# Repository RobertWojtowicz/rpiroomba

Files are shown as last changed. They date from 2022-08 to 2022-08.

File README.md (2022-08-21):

# RPiRoomba

## 1. Introduction
This project is based on the following projects:
- https://github.com/pomeroyb/Create2Control
- https://github.com/silvanmelchior/RPi_Cam_Web_Interface

## 2. How does this work?
- the project applies only to Roomba models that have 7-pin Mini-DIN serial port (iRobot Create Intereface);
- please note that different Roomba models have in different places this port, the PCB was designed for the Roomba 620;
- in case of Roomba 620 you have to cut a hole in the bezel to get to Mini-DIN serial port (the bezel is replaceable, in different colors ;-) to remove the bezel follow the instructions in this project: https://github.com/joric/joirc;
- the port was connected through a logical level converter together with Raspberry Pi Zero W;
- Raspberry Pi Zero W was connected to the camera, LED driver and micro servo, as in the images below:
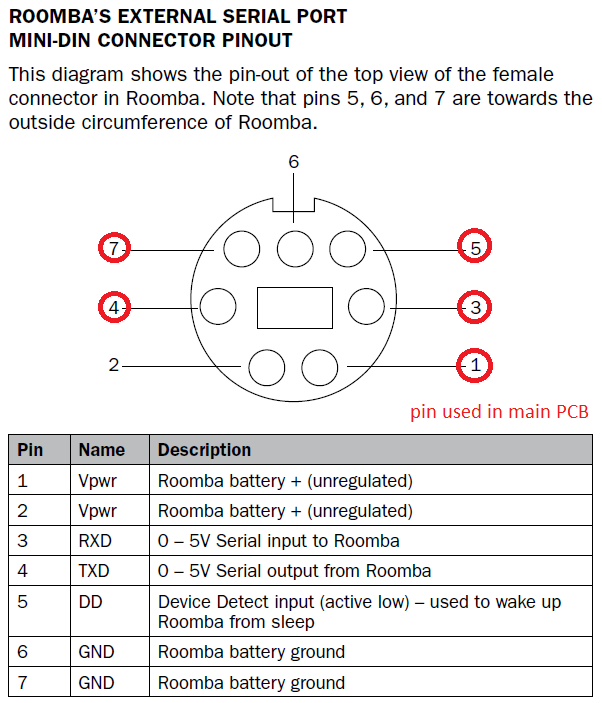
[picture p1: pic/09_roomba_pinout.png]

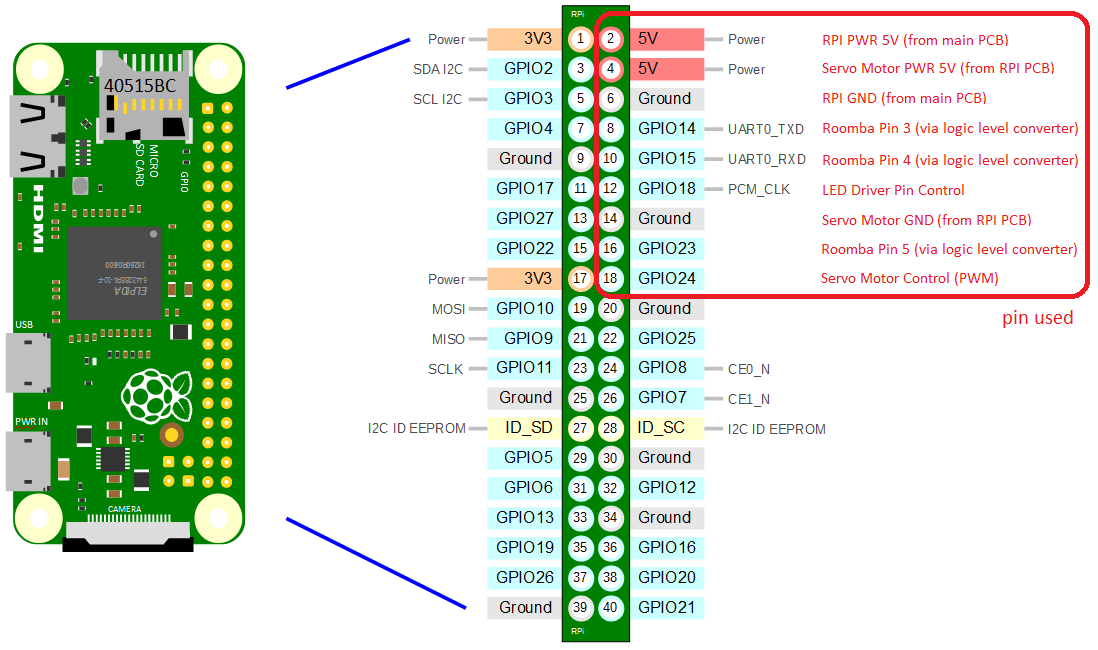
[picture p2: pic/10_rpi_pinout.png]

- the project allows you to remotely control Roomba (via WiFi), watch live video and record, take pictures;
- it is possible to run a cleaning schedule, which Roomba 620 does not have;
- infrared high power LED chip allows visibility of the camera at night;
- it is possible to adjust the camera position angle (0°, 30°, 60°, 90°).

## 3. Build hardware
- create your own PCB v1.1 according to the project files: roomba_led_pcb_v1.sch, roomba_led_pcb_v1.brd, roomba_main_pcb_v1.sh, roomba_main_pcb_v1.brd from this repository (files location: rpiroomba/pcb/), example of finished PCBs v1.0 below:
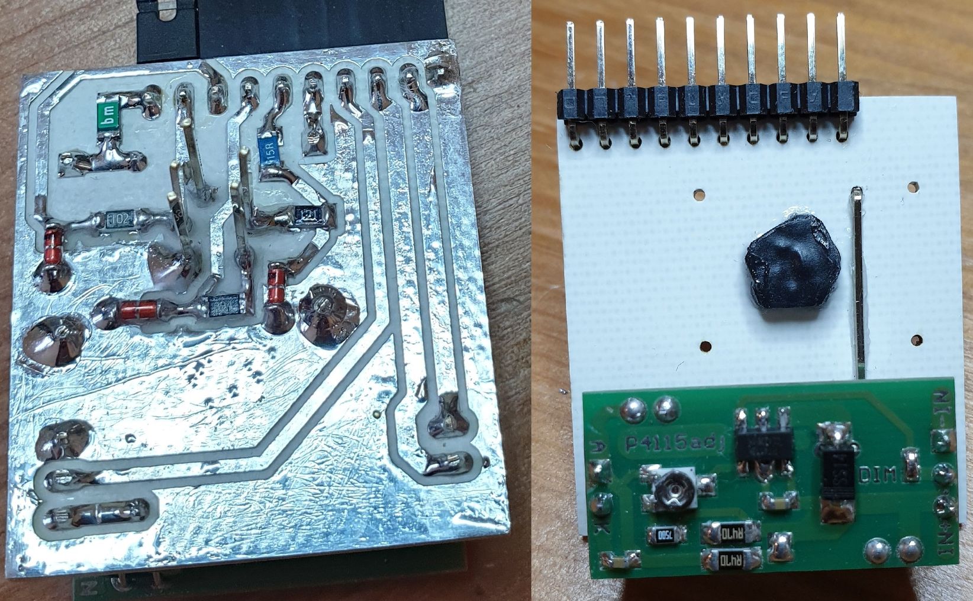
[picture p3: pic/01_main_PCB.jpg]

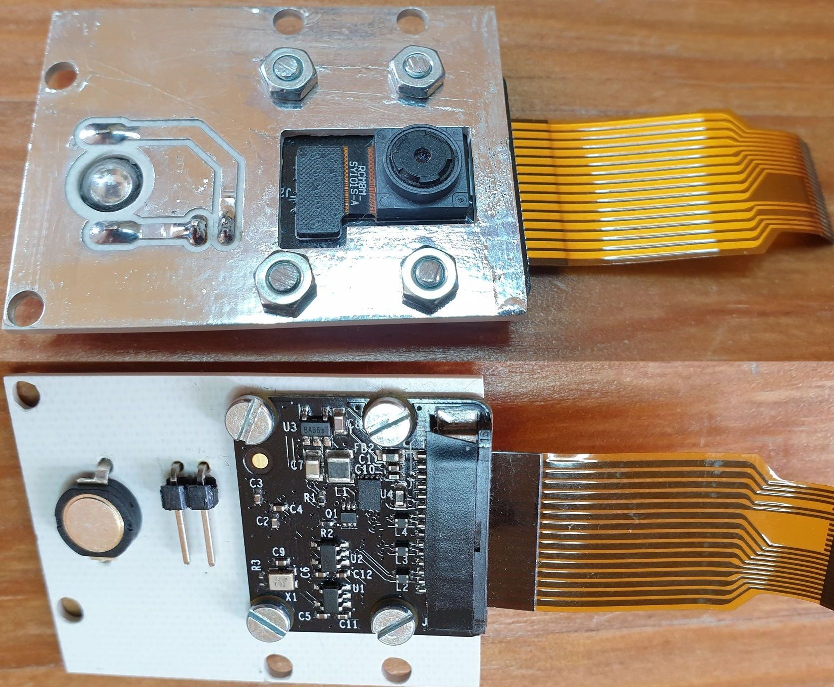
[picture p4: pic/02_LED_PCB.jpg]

- prepare the aluminium housing - heat sink for CPU Raspberry Pi Zero W and high power LED chip, similar to the picture (dimensions approx: 36 mm x 65 mm):
- add a thermal pad under the high power LED chip and the CPU Raspberry Pi Zero W to dissipate the heat to the aluminium case;
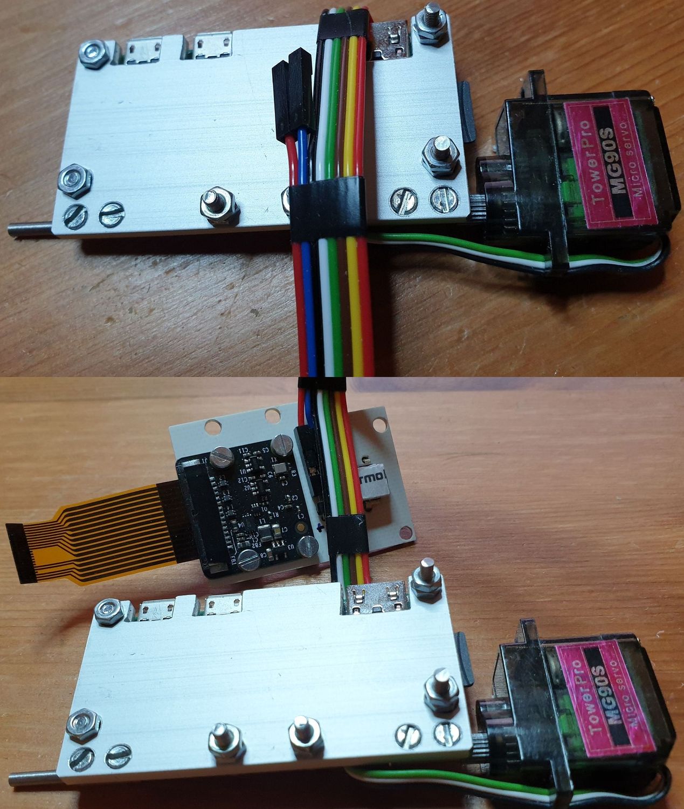
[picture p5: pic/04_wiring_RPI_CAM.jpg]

- the hinges come from the elements of the electric cube;
- metric screws with a diameter of 2 mm were used to connect the parts;
- reduce the current on the LED driver from 700 mA to 230 mA (too high power causes unreadable view);
- set a voltage of 5V on the step-down DC/DC module;
- isolate the Raspberry Pi and camera pins from accidental short circuits, as shown in the following picture:
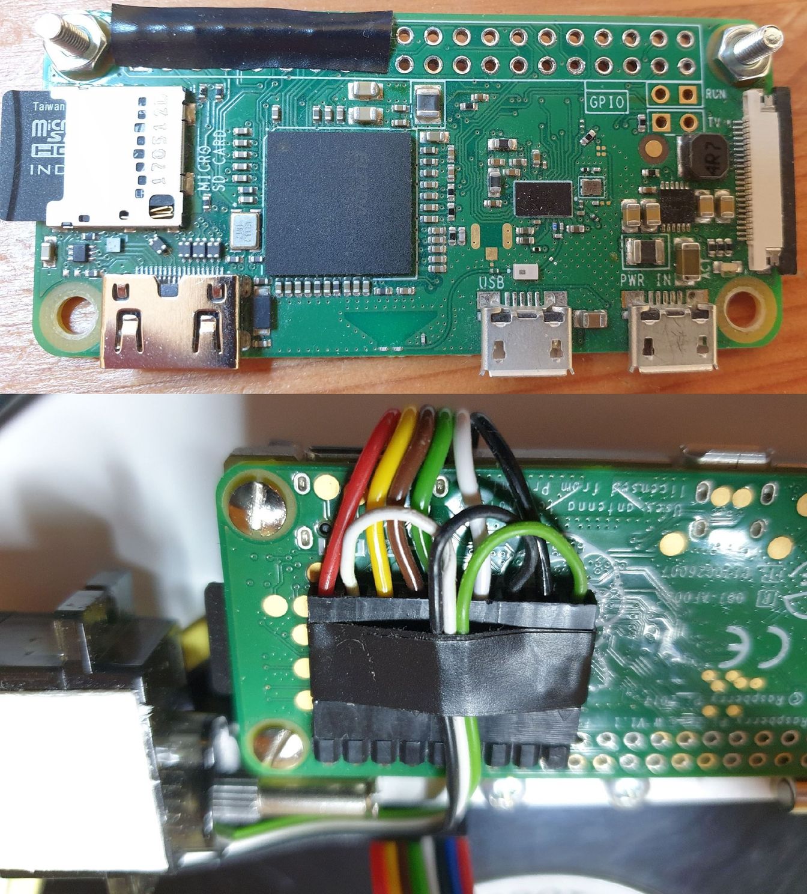
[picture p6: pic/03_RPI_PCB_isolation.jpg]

- isolate the IR sensor on the Roomba in half with tape, as shown in the following picture (otherwise the docking station search algorithm will fail when the Raspberry Pi Zero W module is installed):
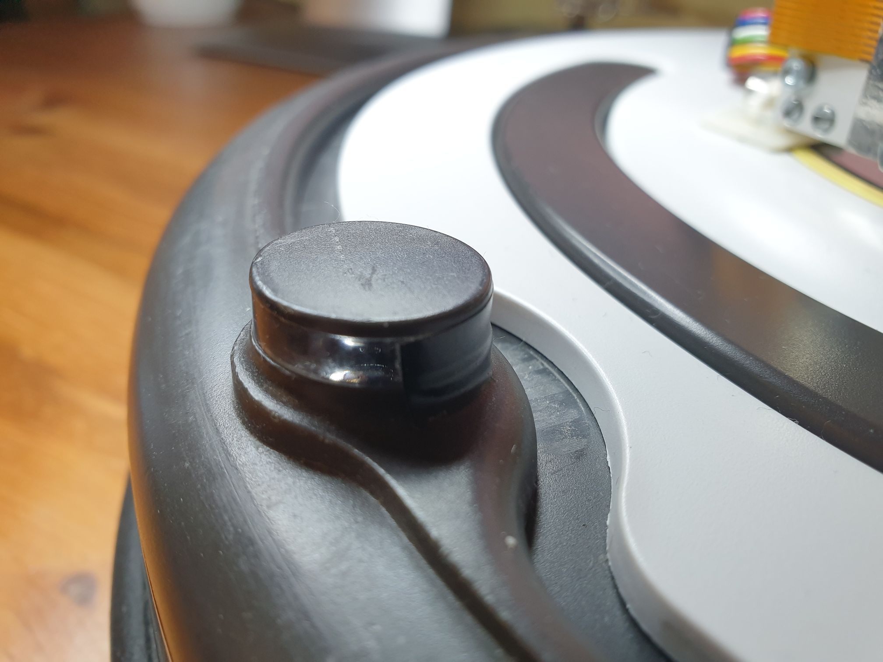
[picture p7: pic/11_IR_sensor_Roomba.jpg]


The following parts are required:
- Modules: 1x DC/DC step-down MP1584EN, 1x Raspberry Pi Zero W V1.1, 1x Raspberry Pi NoIR Camera V2, 1x LED driver PT4115:<br>

- 1x Camera adaptor (cable) from official case Raspberry Pi Zero;
- 1x Micro servo TowerPro MG90S;
- 1x SMD 1206 high power LED chip, 3W IR 850 Nm;
- 1x SMD 1206 resettable polymeric fuse 500 mA;
- 1x SMD 1206 resistors: 15 Ohm, 120 Ohm, 390 Ohm, 1 kOhm;
- 3x SMD 1206 zener diode 3.3 V;
- 1x 40 pin, 2.54 mm, single in line, 20 mm long, header male;
- 1x 40 pin, 2.54 mm, single in line, right angle, header male.

## 4. Preparing Linux system (tested on current kernel 5.15.56+)
- download Raspberry Pi OS (32-bit) Lite system image: https://downloads.raspberrypi.org/raspios_lite_armhf_latest;
- upload system to the microSD card, using Raspberry PI Imager, all you need is a 4 GB microSD card with UHS-1 speed class;
- in Raspberry PI Imager advanced options, set: Enable SSH, Set username and password, Configure wireless LAN;
- on the boot partition replace or edit "config.txt" file based on an example from this repository (file location: /rpi/boot/);
- to disable HDMI (to reduce the power consumption) you must replace or edit "rc.local" file based on an example from this repository (file location: rpiroomba/rpi/etc/);
- install modules: sudo apt-get install python3-pip, sudo pip install pyserial.

## 5. Installing RPi-CAM-Web-Interface (tested on current version 6.6.26)
To install RPi-CAM-Web-Interface, run the following commands:
- sudo apt-get install git;
- git clone https://github.com/silvanmelchior/RPi_Cam_Web_Interface.git;
- cd RPi_Cam_Web_Interface;
- ./install.sh;
- in the configuration menu, clear the "xCam subfolder" option, add the user in "xUser:" admin and the password "xPassword:" and select OK;
- when the installation is complete you can delete folder, rm -rf RPi_Cam_Web_Interface;
- change the autostart parameter to idle in /etc/raspimjpeg (to disable the automatic start of the camera when starting Raspberry Pi);
- change the parameters in the browser under Camera Settings to: Load Preset: HD-ready 720p, Rotation: Rotate_270, Preview quality: Quality: 10, Width 1280, Divider: 1, for example picture of RPI Cam interface:
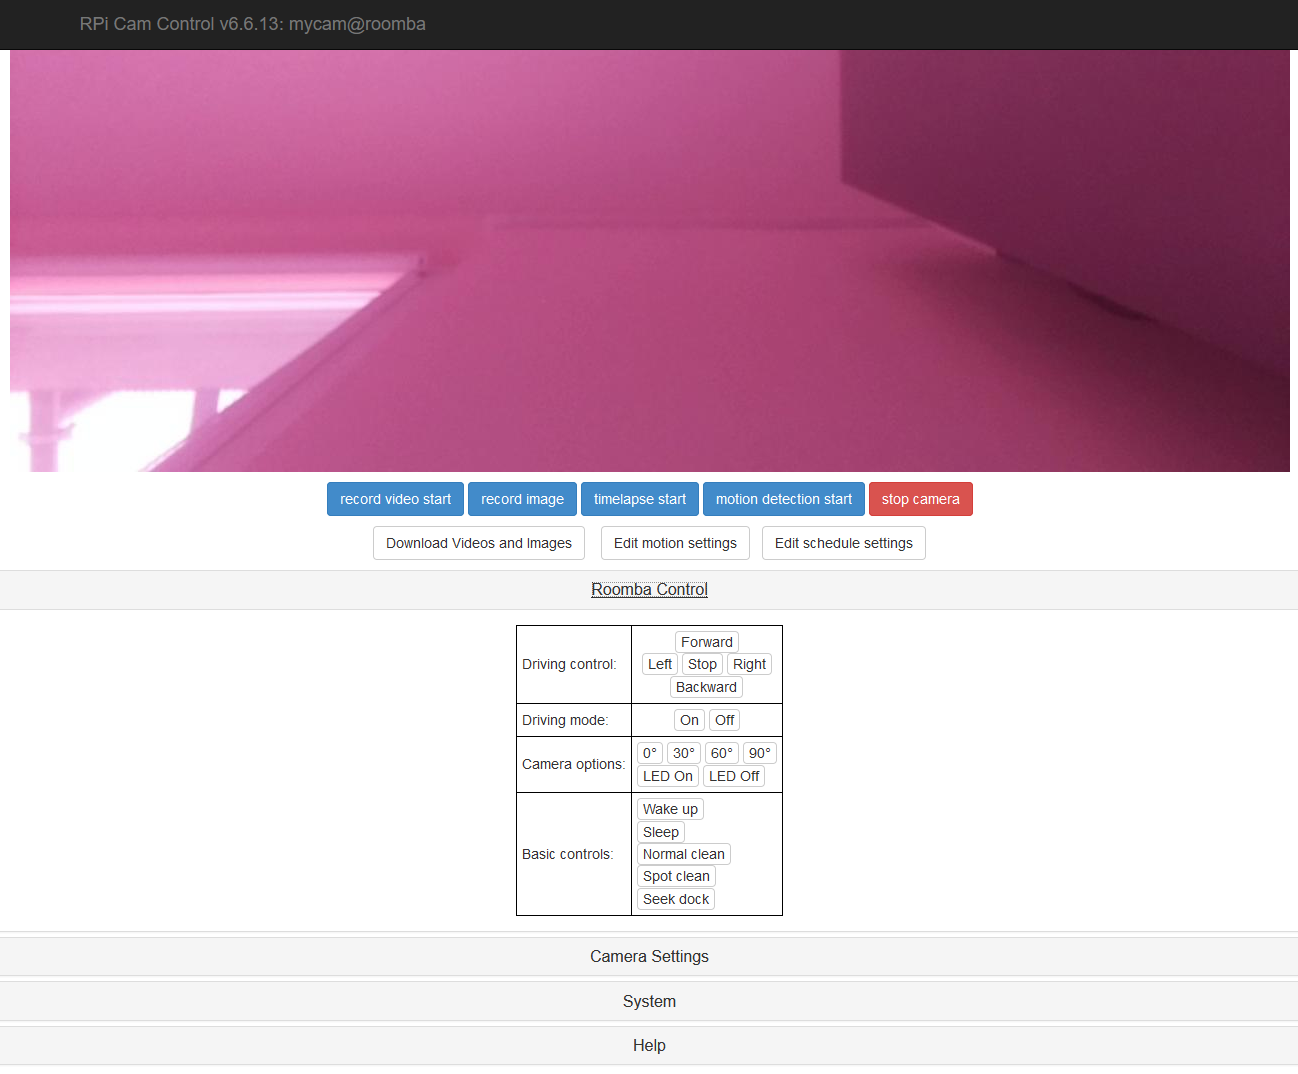
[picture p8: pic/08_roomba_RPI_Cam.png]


## 6. Configuring scripts
- create a roomba folder in /var/www/ directory and then copy the files, e.g. using WinSCP from this repository (file location: /rpi/www/roomba/): command.php, config.json, create2api.py, jquery-3.6.0.min.js, roomba.py, submit.js;
- in /var/www/ directory, you should replace index.html from this repository (file location: /rpi/www/);
- grant permissions for user-data: sudo usermod -a -G gpio www-data, sudo usermod -a -G gpio $USER, sudo usermod -a -G dialout www-data;
- grant permissions to execute files, chmod +x /var/www/roomba/*

## 7. Creating a cleaning schedule
- Roomba 620 does not have its own cleaning schedule, but you can add in cron;
- for example, Monday, Wednesday, Friday at 12:00 you should edit the file using the command crontab -e:<br/> 
00 12 * * 1 python3 /var/www/roomba/roomba.py clean<br/>
00 12 * * 3 python3 /var/www/roomba/roomba.py clean<br/>
00 12 * * 5 python3 /var/www/roomba/roomba.py clean

## 8. Some final project photos
- Camera down (position angle 0°):
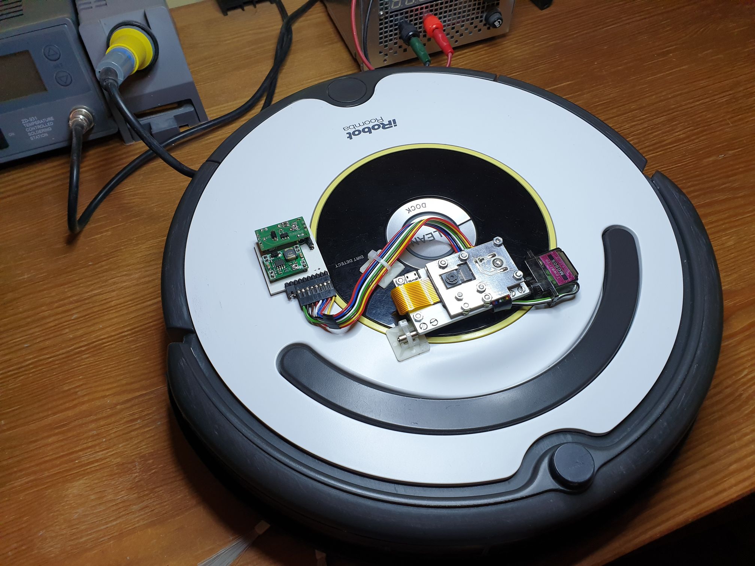
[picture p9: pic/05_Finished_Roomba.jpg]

- Current limit adjustment on LED driver:
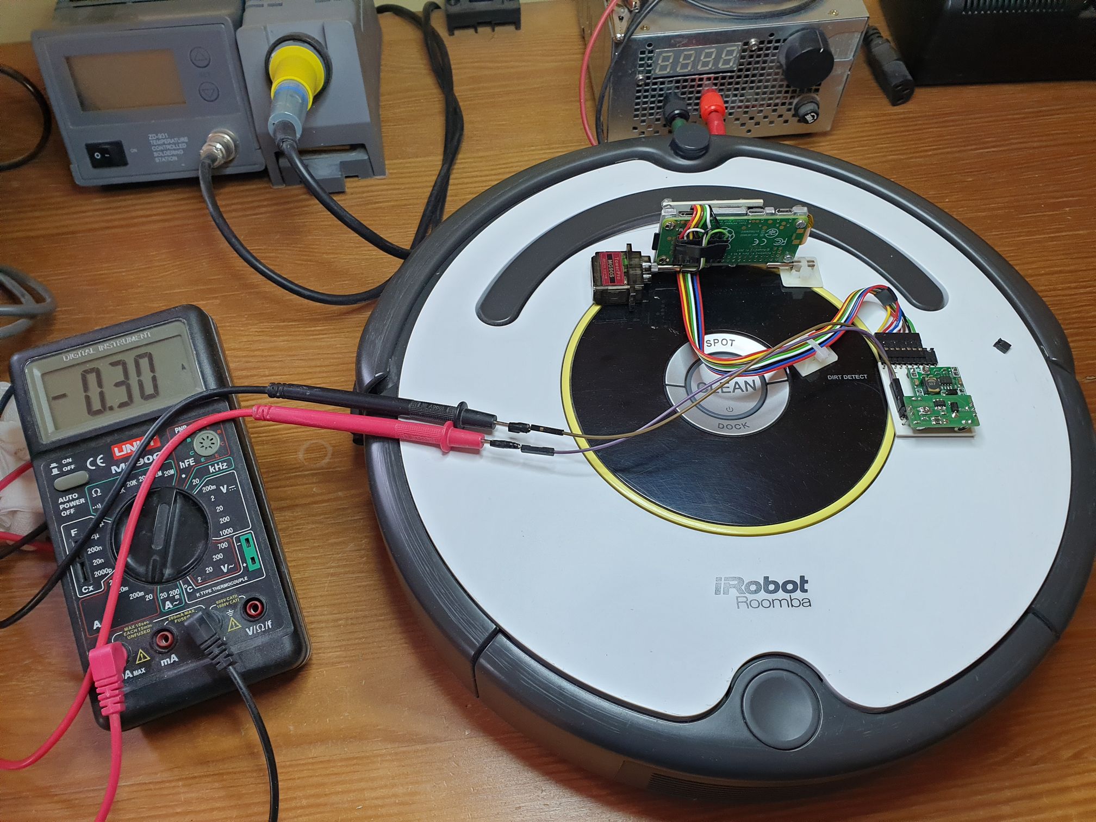
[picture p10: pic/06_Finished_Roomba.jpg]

- Camera up (position angle 90°):
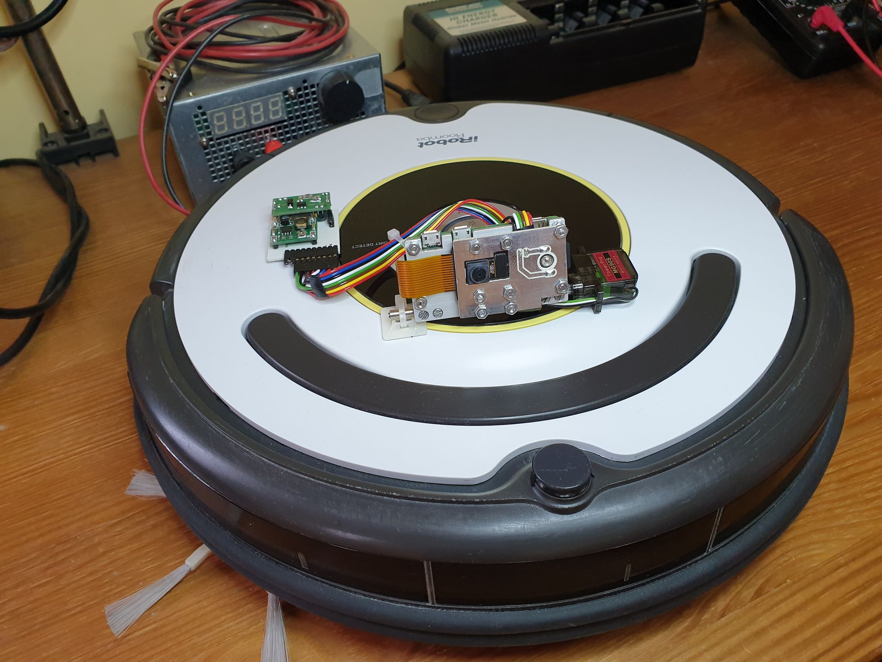
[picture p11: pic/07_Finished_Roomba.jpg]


<a href="https://www.buymeacoffee.com/RobertWojtowicz" target="_blank">Buy Me A Coffee</a>

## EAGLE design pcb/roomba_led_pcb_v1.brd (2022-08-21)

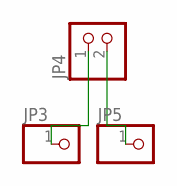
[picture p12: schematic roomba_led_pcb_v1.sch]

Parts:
JP3, JP5: PINHD-1X1; 1X01
JP4: PINHD-1X2/90; 1X02/90

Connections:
unnamed: JP3.1, JP4.1
unnamed: JP4.2, JP5.1

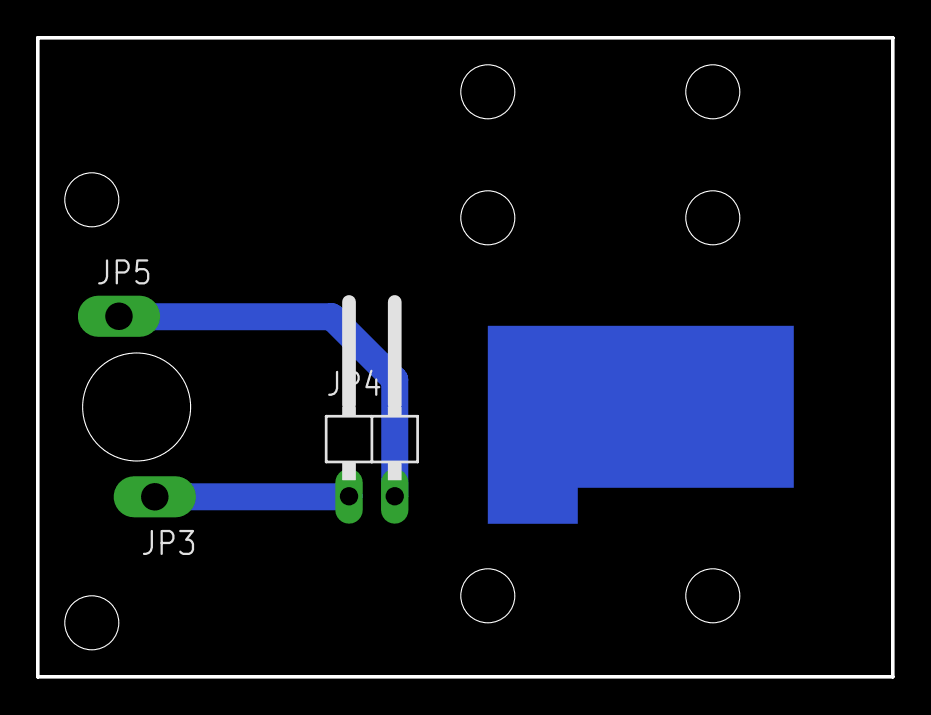
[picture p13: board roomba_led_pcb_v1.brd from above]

Board: 2 copper layers, 47.5 x 35.5 mm, 3 parts (0 on the bottom side), 2 nets.

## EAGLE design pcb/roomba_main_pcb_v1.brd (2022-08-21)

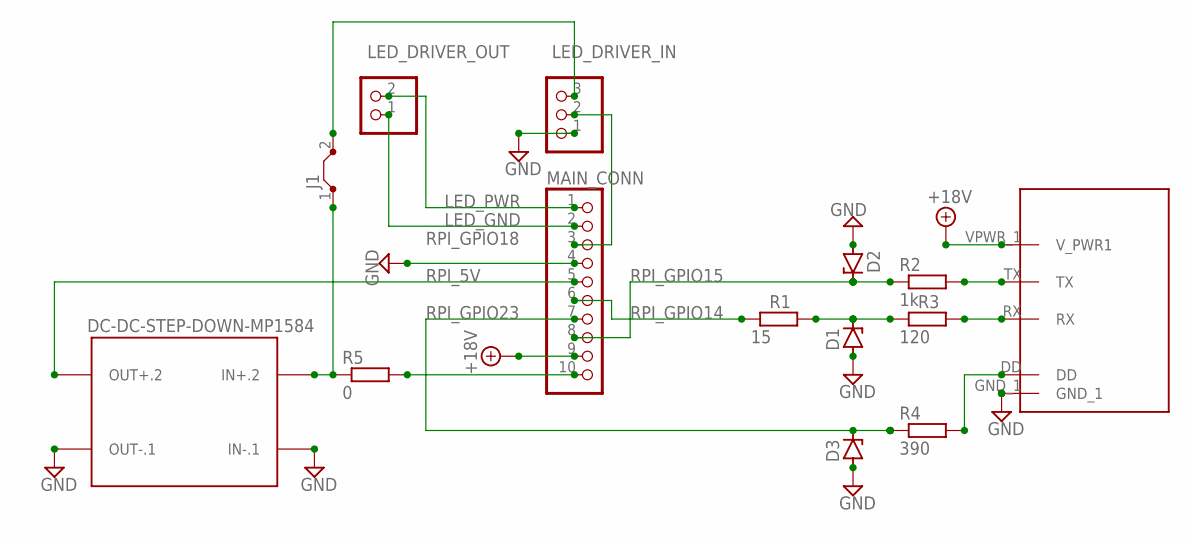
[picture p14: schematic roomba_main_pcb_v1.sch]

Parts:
D1, D2, D3: ZENER-DIODESOD80C; SOD80C
J1: J25MM; 25
LED_DRIVER_IN: PINHD-1X3; 1X03
LED_DRIVER_OUT: PINHD-1X2; 1X02
MAIN_CONN: PINHD-1X10/90; 1X10/90
R1: 15; M1206
R2: 1k; M1206
R3: 120; M1206
R4: 390; M1206
R5: 0; M1206
ROOMBA_PORT: 7_PIN; PIN-7
U$1: DC-DC-STEP-DOWN-MP1584

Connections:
+18V: MAIN_CONN.9, ROOMBA_PORT.VPWR_1 (V_PWR1)
GND: D1.A, D2.A, D3.A, LED_DRIVER_IN.1, MAIN_CONN.4, ROOMBA_PORT.GND_1, U$1.IN-.1, U$1.OUT-.1
LED_GND: LED_DRIVER_OUT.1, MAIN_CONN.2
LED_PWR: LED_DRIVER_OUT.2, MAIN_CONN.1
unnamed: J1.1, R5.1, U$1.IN+.2
unnamed: R4.2, ROOMBA_PORT.DD
unnamed: J1.2, LED_DRIVER_IN.3
unnamed: R3.2, ROOMBA_PORT.RX
unnamed: D1.C, R1.2, R3.1
unnamed: R2.2, ROOMBA_PORT.TX
unnamed: MAIN_CONN.10, R5.2
RPI_5V: MAIN_CONN.5, U$1.OUT+.2
RPI_GPIO14: MAIN_CONN.6, R1.1
RPI_GPIO15: D2.C, MAIN_CONN.8, R2.1
RPI_GPIO18: LED_DRIVER_IN.2, MAIN_CONN.3
RPI_GPIO23: D3.C, MAIN_CONN.7, R4.1

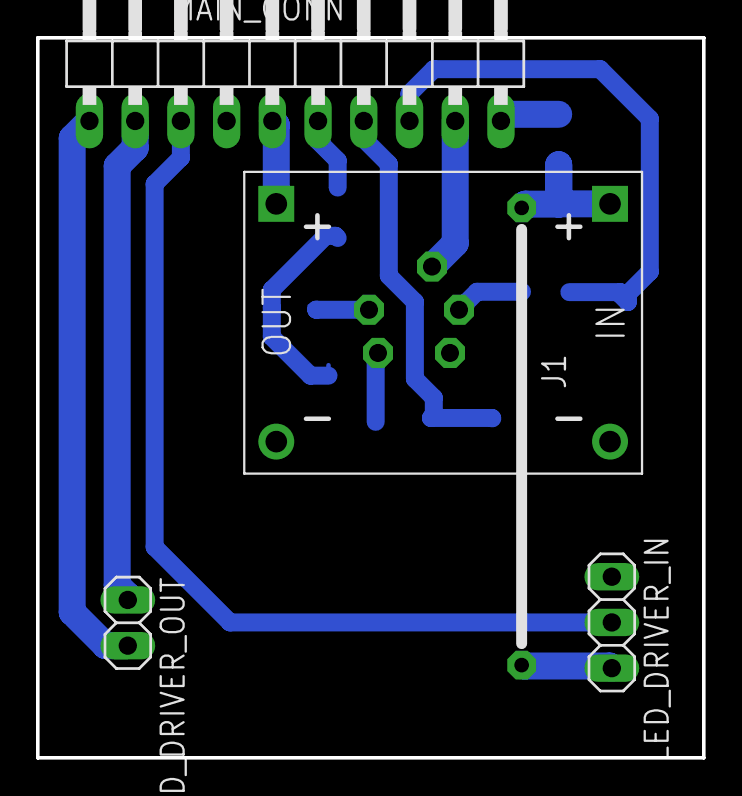
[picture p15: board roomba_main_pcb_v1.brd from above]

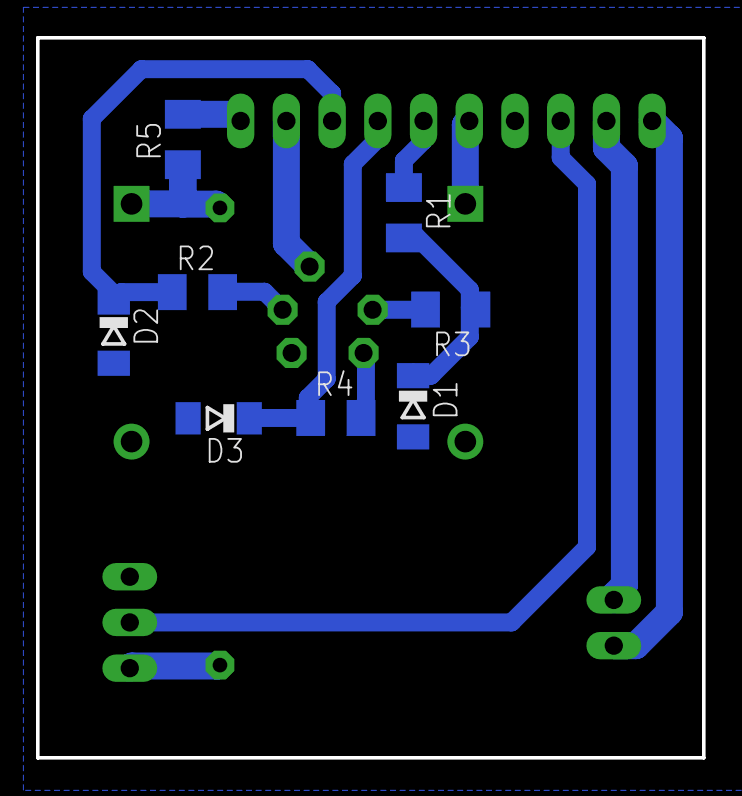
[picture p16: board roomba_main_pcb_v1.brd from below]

Board: 2 copper layers, 37.0 x 40.0 mm, 14 parts (8 on the bottom side), 16 nets.

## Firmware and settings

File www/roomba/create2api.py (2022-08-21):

#!/usr/bin/python

# Update to python3 for RPiRoomba v1.1

import json
import serial
import struct
import os
import warnings
import time

class Error(Exception):
    """Error"""
    pass

def custom_format_warning(message, category, filename, lineno, file=None, line=None):
    return 'Line ' + str(lineno) + ': ' + str(message) + '\n'
    #return ' %s:%s: %s:%s' % (filename, lineno, category.__name__, message)
    
class ROIDataByteError(Error):
    """Exception raised for errors in ROI data bytes.

        Attributes:
            msg -- explanation of the error
    """
    
    def __init__(self, msg):
        self.msg = msg

class ROIFailedToSendError(Error):
    """Exception raised when an error in data bytes prevented a packet to be sent

        Attributes:
            msg -- explanation of the error    
    """
    def __init__(self, msg):
        self.msg = msg

class ROIFailedToReceiveError(Error):
    """Exception raised when there is an error in the data received from the Create 2

        Attributes:
            msg -- explanation of the error
    """
    def __init__(self,msg):
        self.msg = msg


        
class Config(object):
    """This class handles loading and saving config files that store the
        Opcodes and other useful dicts
    
    """
    
    def __init__(self):
        self.fname = '/var/www/roomba/config.json'
        self.data = None
    
    def load(self):
        """ Loads a Create2 config file, that holds various dicts of opcodes.
        
        """
        if os.path.isfile(self.fname):
            #file exists, load it
            with open(self.fname) as fileData:
                try:
                    self.data = json.load(fileData)
                    print ('Loaded config and opcodes')
                except ValueError('e'):
                    print ('Could not load config')
        else:
            #couldn't find file
            print('No config file found')
            raise ValueError('Could not find config')

class SerialCommandInterface(object):
    """This class handles sending commands to the Create2.

    """

    def __init__(self):
        com = '/dev/ttyAMA0'  #This should not be hard coded...
        baud = 115200
        
        self.ser = serial.Serial()
        self.ser.port = com
        self.ser.baudrate = baud
        print(self.ser.name)
        if self.ser.isOpen(): 
            print('port was open')
            self.ser.close()
        self.ser.open()
        print('opened port')
    
    def send(self, opcode, data):
        #First thing to do is convert the opcode to a tuple.
        temp_opcode = (opcode,)
        bytes = None
        
        if data == None:
            #Sometimes opcodes don't need data. Since we can't add
            # a None type to a tuple, we have to make this check.
            bytes = temp_opcode
        else:
            #Add the opcodes and data together
            bytes = temp_opcode + data
        #print bytes
        self.ser.write(struct.pack('B' * len(bytes), *bytes))
    
    def Read(self, num_bytes):
        """Read a string of 'num_bytes' bytes from the robot.

            Arguments:
                num_bytes: The number of bytes we expect to read.
        """
        #logging.debug('Attempting to read %d bytes from SCI port.' % num_bytes)
        data = self.ser.read(num_bytes)
        #logging.debug('Read %d bytes from SCI port.' % len(data))
        if not data:
            raise ROIFailedToReceiveError('Error reading from SCI port. No data.')
        if len(data) != num_bytes:
            raise ROIFailedToReceiveError('Error reading from SCI port. Wrong data length.')
        return data

    def Close(self):
        """Closes the serial connection.
        """
        self.ser.close()

class Create2(object):
    """The top level class for controlling a Create2.
        This is the only class that outside scripts should be interacting with.

    """

    def __init__(self):
  
        self.SCI = SerialCommandInterface()
        self.config = Config()
        self.config.load()
        self.decoder = sensorPacketDecoder(dict(self.config.data['sensor group packet lengths']))
        self.sensor_state = dict(self.config.data['sensor data']) # Load a raw sensor dict. None of these values are correct.
        self.sleep_timer = .5  
    
    def destroy(self):
        """Closes up serial ports and terminates connection to the Create2
        """
        self.SCI.Close()
        print('Disconnected')

    """ START OF OPEN INTERFACE COMMANDS
    """
    def start(self):
        self.SCI.send(self.config.data['opcodes']['start'], None)

    def reset(self):
        self.SCI.send(self.config.data['opcodes']['reset'], None)

    def stop(self):
        self.SCI.send(self.config.data['opcodes']['stop'], None)

    def baud(self, baudRate):
        baud_dict = {
            300:0,
            600:1,
            1200:2,
            2400:3,
            4800:4,
            9600:5,
            14400:6,
            19200:7,
            28800:8,
            38400:9,
            57600:10,
            115200:11
            }
        if baudRate in baud_dict:
            self.SCI.send(self.config.data['opcodes']['baud'], tuple(baud_dict[baudRate]))
        else:
            raise ROIDataByteError("Invalid buad rate")

    def safe(self):
        """Puts the Create 2 into safe mode. Blocks for a short (<.5 sec) amount of time so the
            bot has time to change modes.
        """
        self.SCI.send(self.config.data['opcodes']['safe'], None)
        time.sleep(self.sleep_timer)

    def full(self):
        """Puts the Create 2 into full mode. Blocks for a short (<.5 sec) amount of time so the
            bot has time to change modes.
        """
        self.SCI.send(self.config.data['opcodes']['full'], None)
        time.sleep(self.sleep_timer)

    def clean(self):
        self.SCI.send(self.config.data['opcodes']['clean'], None)

    def max(self):
        self.SCI.send(self.config.data['opcodes']['max'], None)

    def spot(self):
        self.SCI.send(self.config.data['opcodes']['spot'], None)

    def seek_dock(self):
        self.SCI.send(self.config.data['opcodes']['seek_dock'], None)

    def power(self):
        self.SCI.send(self.config.data['opcodes']['power'], None)

    def schedule(self):
        """Not implementing this for now.
        """    
        #self.SCI.send(self.config.data['opcodes']['start'],0)
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

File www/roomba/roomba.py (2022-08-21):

# *********
# RPiRoomba v1.0
# *********

import create2api
import RPi.GPIO as GPIO
from time import sleep
from sys import argv

# Driving control:
def forward():
    bot = create2api.Create2()
    bot.drive_straight(200) #Normal speed of Roomba is 280

def left():
    bot = create2api.Create2()
    bot.turn_clockwise(-11)
    sleep(0.5)
    bot.drive_straight(0)

def stop():
    bot = create2api.Create2()
    bot.drive_straight(0)
	
def right():
    bot = create2api.Create2()
    bot.turn_clockwise(11)
    sleep(0.5)
    bot.drive_straight(0)

def backward():
    bot = create2api.Create2()
    bot.drive_straight(-200) #Normal speed of Roomba is -280

# Driving mode:
def open():
    bot = create2api.Create2()
    bot.start()
    bot.safe()

def close():
    bot = create2api.Create2()
    bot.stop()

# Camera options:
def camera_0():
    GPIO.setmode(GPIO.BCM)
    GPIO.setup(24, GPIO.OUT)
    servo = GPIO.PWM(24, 50)
    servo.start(0)
    servo.ChangeDutyCycle(2 + (90 / 18))
    sleep(0.5)
    servo.ChangeDutyCycle(0)
    servo.stop()
    GPIO.cleanup()

def camera_30():
    GPIO.setmode(GPIO.BCM)
    GPIO.setup(24, GPIO.OUT)
    servo = GPIO.PWM(24, 50)
    servo.start(0)
    servo.ChangeDutyCycle(2 + (60 / 18))
    sleep(0.5)
    servo.ChangeDutyCycle(0)
    servo.stop()
    GPIO.cleanup()

def camera_60():
    GPIO.setmode(GPIO.BCM)
    GPIO.setup(24, GPIO.OUT)
    servo = GPIO.PWM(24, 50)
    servo.start(0)
    servo.ChangeDutyCycle(2 + (30 / 18))
    sleep(0.5)
    servo.ChangeDutyCycle(0)
    servo.stop()
    GPIO.cleanup()

def camera_90():
    GPIO.setmode(GPIO.BCM)
    GPIO.setup(24, GPIO.OUT)
    servo = GPIO.PWM(24, 50)
    servo.start(0)
    servo.ChangeDutyCycle(2 + (0 / 18))
    sleep(0.5)
    servo.ChangeDutyCycle(0)
    servo.stop()
    GPIO.cleanup()
	
def led_on():
	GPIO.setwarnings(False)
	GPIO.setmode(GPIO.BCM)
	GPIO.setup(18, GPIO.OUT)
	GPIO.cleanup()

def led_off():
	GPIO.setmode(GPIO.BCM)
	GPIO.setup(18, GPIO.OUT)
	GPIO.output(18, 0)

# Basic controls:
def wake_up():
    GPIO.setmode(GPIO.BCM)
    GPIO.setup(23, GPIO.OUT)
    GPIO.output(23, GPIO.HIGH)
    sleep(1)
    GPIO.output(23, GPIO.LOW)
    sleep(1)
    GPIO.output(23, GPIO.HIGH)
    GPIO.cleanup()

def go_sleep():
    bot = create2api.Create2()
    bot.start()
    bot.power()
    bot.stop()

def clean():
    bot = create2api.Create2()
    bot.start()
    bot.clean()
    bot.stop()

def spot():
    bot = create2api.Create2()
    bot.start()
    bot.spot()
    bot.stop()

def dock():
    bot = create2api.Create2()
    bot.start()
    bot.seek_dock()
    bot.stop()

_, function_name = argv
locals()[function_name]()

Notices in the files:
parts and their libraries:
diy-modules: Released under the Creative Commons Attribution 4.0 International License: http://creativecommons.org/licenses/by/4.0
